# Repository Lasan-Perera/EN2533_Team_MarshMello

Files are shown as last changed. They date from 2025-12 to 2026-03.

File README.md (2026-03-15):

# Team MarshMello 
## Module: EN2533 Robot Design and Competition

## 📖 Project Overview
Our robot was developed to complete multiple challenges announced two months before the competition. These challenges included line following, maze solving, box handling, ramp climbing, dashed-line navigation, barcode detection, ball pickup, wall following, arrow-based navigation, and ball shooting. The project required significant hardware and software development, and the final robot was able to autonomously navigate the arena and successfully complete the assigned tasks.

## 🤖 Robot
file_00000000e0a47206bf88b3c999087ba9



## 🎥 Robot Task Demonstration
Robot Tasks Video (https://youtu.be/oBLyfxPuTzA)

## 🔧 Robot Hardware Specifications
- **Max Dimensions**: 200mm × 190mm  
- **Power Supply**: 4 18650 Li-ion Battries
- **Components**:
  - Arduino Mega mini Development board x1
  - Raykha S8 – TCRT5000 based 8-channel reflective sensor array x1
  - Nema 17 Stepper Motors x2
  - DRV8825 Stepper Driver x2
  - LM2596 DC-DC Buck Converter x2
  - XL4015 DC-DC Buck Converter x1
  - MG90 metal gear servo motors x3
  - MG995 Tower Pro servo motor x1
  - SHARP GP2Y0A51SK0F Infrared IR Sensor x5
  - TCS34725 RGB Colour Recognition Sensor x1
  - Obstacle Avoidance Sensor IR Infrared Module x3
  - DC Motor 380 Motor x2
  - Rotary Encoder Module with Push Button
  - 0.96″ OLED display

## 💻 Robot Software Specifications
- **Programming Language**: C++
- **IDE**: Arduino IDE
- **Libraries**:
  - Arduino.h
  - Servo.h
  - Adafruit_TCS34725.h
  - MultiStepper.h
  - AccelStepper.h
  - Wire.h
  - Adafruit_GFX
  - Adafruit_SSD1306
- **3D Modelling**: AutoDesk Fusion
- **Schemetic Design**: Altium Designer



  




## ⚙️ Mechanisms and Algorithms
### <u>Custom Motor Brackets, Wheel Rims, SHARP IR Brackets</u>



---

### <u>Balls and Box Pickup Mechanism</u>

From the beginning, we decided to use an arm mechanism to pick up balls and boxes from the side. This required precise control of the robot. We planned to store the collected balls in a container located at the top of the robot. The container had to be positioned at an appropriate height so gravity could be used to feed the balls into the ball-sending mechanism, which was a major design challenge.

To address this, we used an L-shaped arm. A high-torque servo was used for the main arm movement, while a smaller servo controlled the gripper. This combination significantly simplified the mechanism.

The gripper had to handle both balls (4 cm diameter) and boxes (5 cm wide). To achieve this, I designed a special gripper with an internal cutout. When gripping a ball, the arms move closer than usual, allowing the ball to travel upward through the rail-like cut. Since the color sensor was placed at the top, this design allowed us to take color readings effectively.

However, the initial grip was not strong enough to hold boxes securely. To improve grip, we added hot glue inside the gripper and covered it with a rubber balloon. While this solved the box-gripping issue, it prevented the ball from moving upward.

To overcome this, we implemented a control solution: after gripping the ball and raising the arm, the gripper briefly opens and closes again. This allows the ball to move closer to the color sensor. This approach worked successfully.



---

### <u>Balls Storing Mechanism</u>

The container had to be positioned at a suitable height so gravity could feed the balls into the ball-sending mechanism. The main challenge was designing a container within limited space that could store four balls while ensuring they would not block each other during release.

Later, I discovered that the original container design was approximately 5 mm lower than the required height. To fix this, I added a 5 mm thick 3D-printed spacer block in the middle of the structure.



---

### <u>Balls Shooting Mechanism</u>

The ball sender needed to launch the balls through a given hoop. We used DC motors rotating at high speed, with the ball placed between them. To achieve sufficient grip, we used two toy truck wheels attached to the motors.

Finding the correct distance between the motors required several design iterations. Another major issue was ensuring that balls were sent one at a time. If two balls entered the mechanism simultaneously, the second ball would not travel the required distance.

To solve this, I designed a blocking mechanism that prevents the next ball from entering while one ball is being launched.

Initially, we attempted to control the motors using relays, but this failed due to the high startup current. When the motors started, the relay would switch off, causing an endless on-off loop without proper motor operation. To resolve this issue, we replaced the relays with a motor driver, which worked reliably.



---

### <u>Grid Solving Algorithm</u>

The robot operates on a **Grid Navigation System** driven by a finite state machine.

- **Mapping**: Maintains an internal 8×8 coordinate grid updated in real time using wall and object detection.
- **Pathfinding**: Uses **Breadth-First Search (BFS)** to compute the shortest path to any target cell. The path is recalculated after each movement to adapt to new obstacles.
- **Mission Logic**: Controlled by a high-level **State Machine**:
  - **Search**: Snake-pattern sweep of the grid to locate boxes
  - **Pickup**: Multi-angle selector enforcing strict X-axis approach based on arm geometry
  - **Transport**: BFS-based navigation back to the sanctuary zone
  - **Avoidance**: Marks inaccessible paths and targets to prevent deadlocks

## 🚩 Competition Tasks
- **Task 1**: The Labyrinth of Shadows (Grid Solving) 
- **Task 2**: The Ramp of Trials (Creation, Ascending, and Descending Ramp)
- **Task 3**: The Oracle of Runes (Barcode Reading)
- **Task 4**: The Circular Fortress (Wall Following and Ball Collection)
- **Task 5**: The Wall of Whispers & Pendulum of Doom 
- **Task 6**: The Line of Destiny & The Ring of Triumph (Shooting Task)

**Project Documentation**
[]([path/to/your-file.pdf](https://github.com/user-attachments/files/24347659/Robot_Design_Task_2025_251226_191908.pdf)) 

## 🏟️ Arena


## 👥 Team Members
| Name | Index Number |
|---|---|
| Lasan Sanjula Perera | 230487D |
| Hasith Nettikumara | 230436X |
| Kavija Karunarathna | 230322U |
| Hiruna Kariyawasam | 230318M |
| Rusiru Anupama | 230536E |



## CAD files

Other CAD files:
3D_Files/Assembly.f3z

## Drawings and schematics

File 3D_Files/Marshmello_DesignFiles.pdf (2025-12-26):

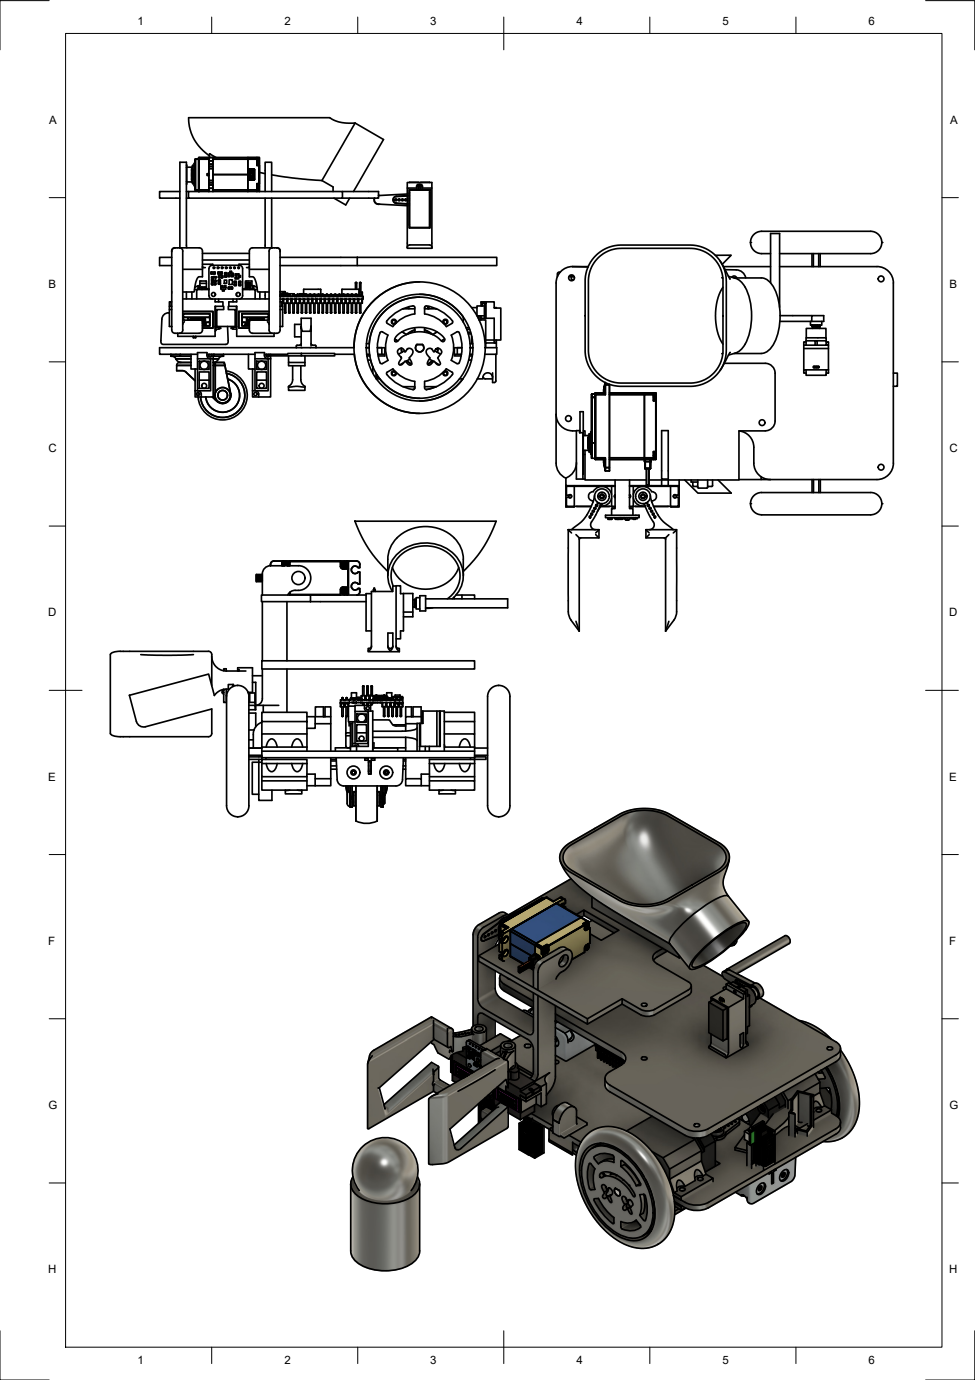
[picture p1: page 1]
6 ABCDEFGH; ABCDEFGH

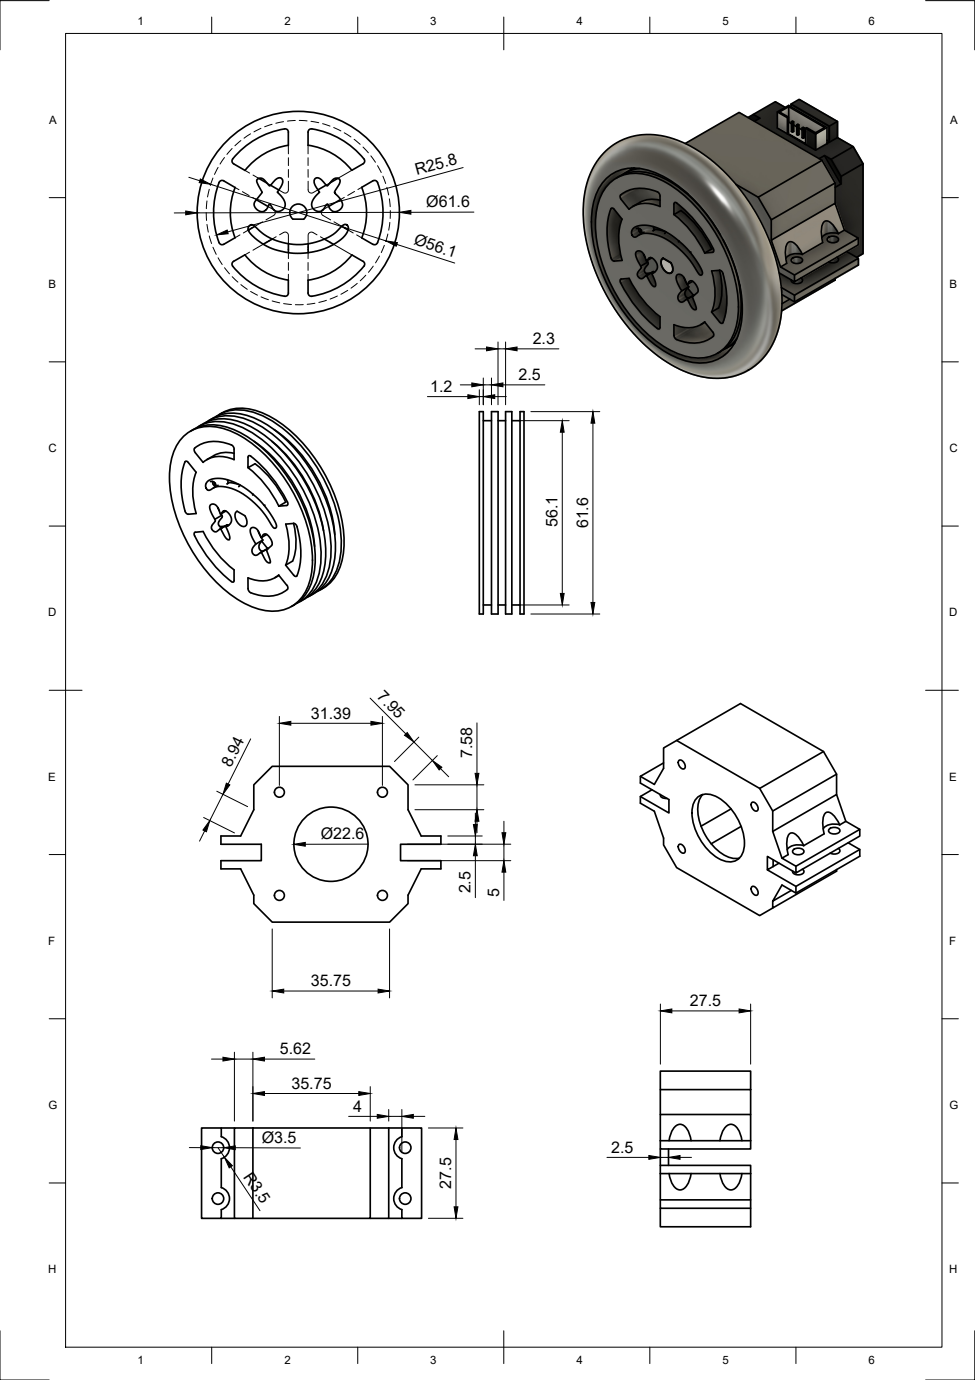
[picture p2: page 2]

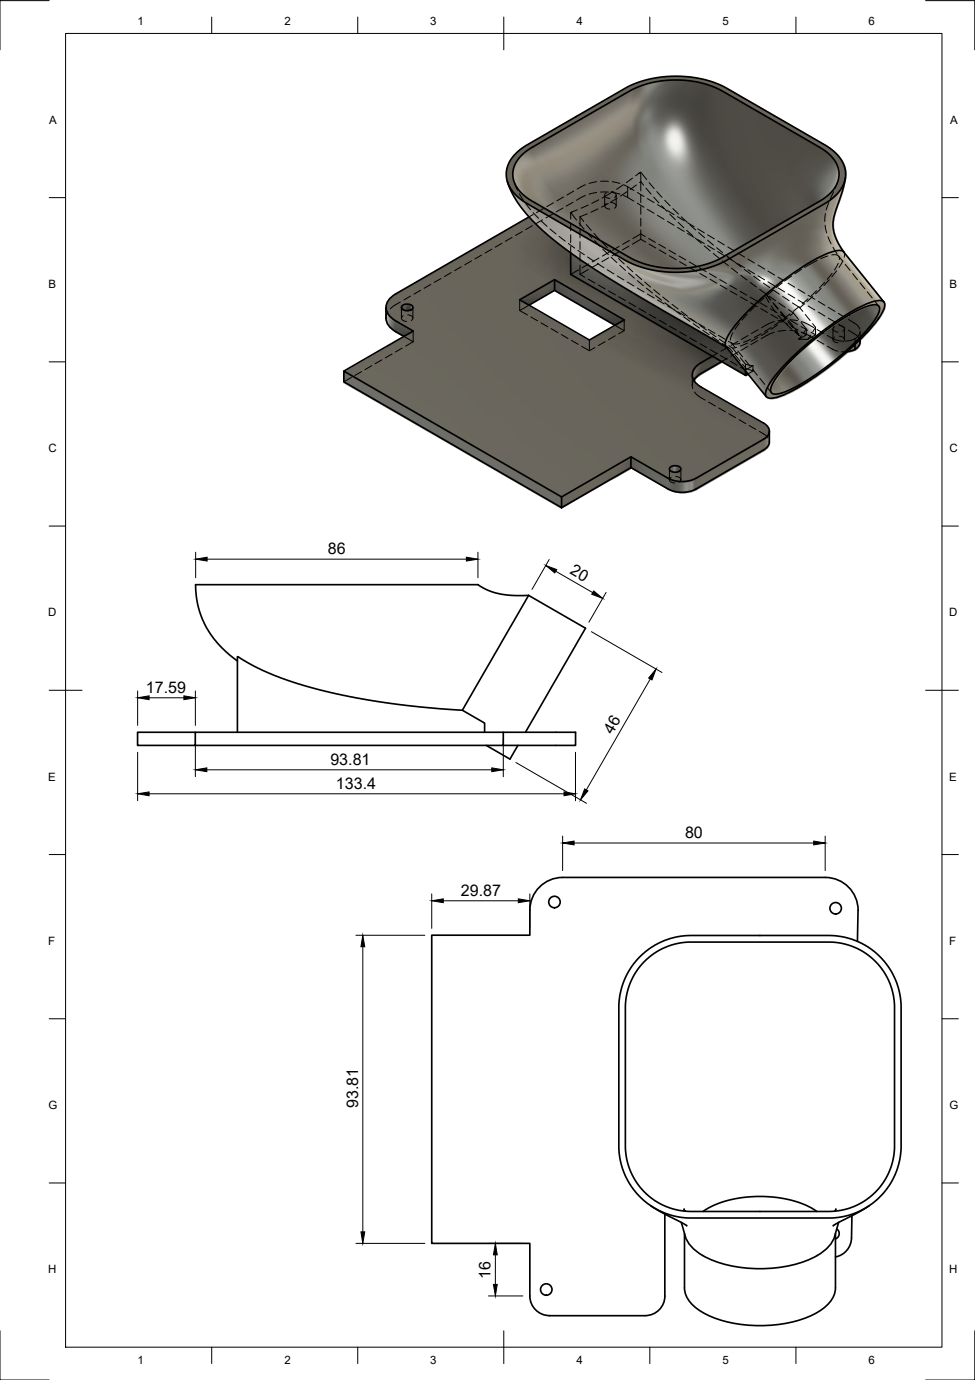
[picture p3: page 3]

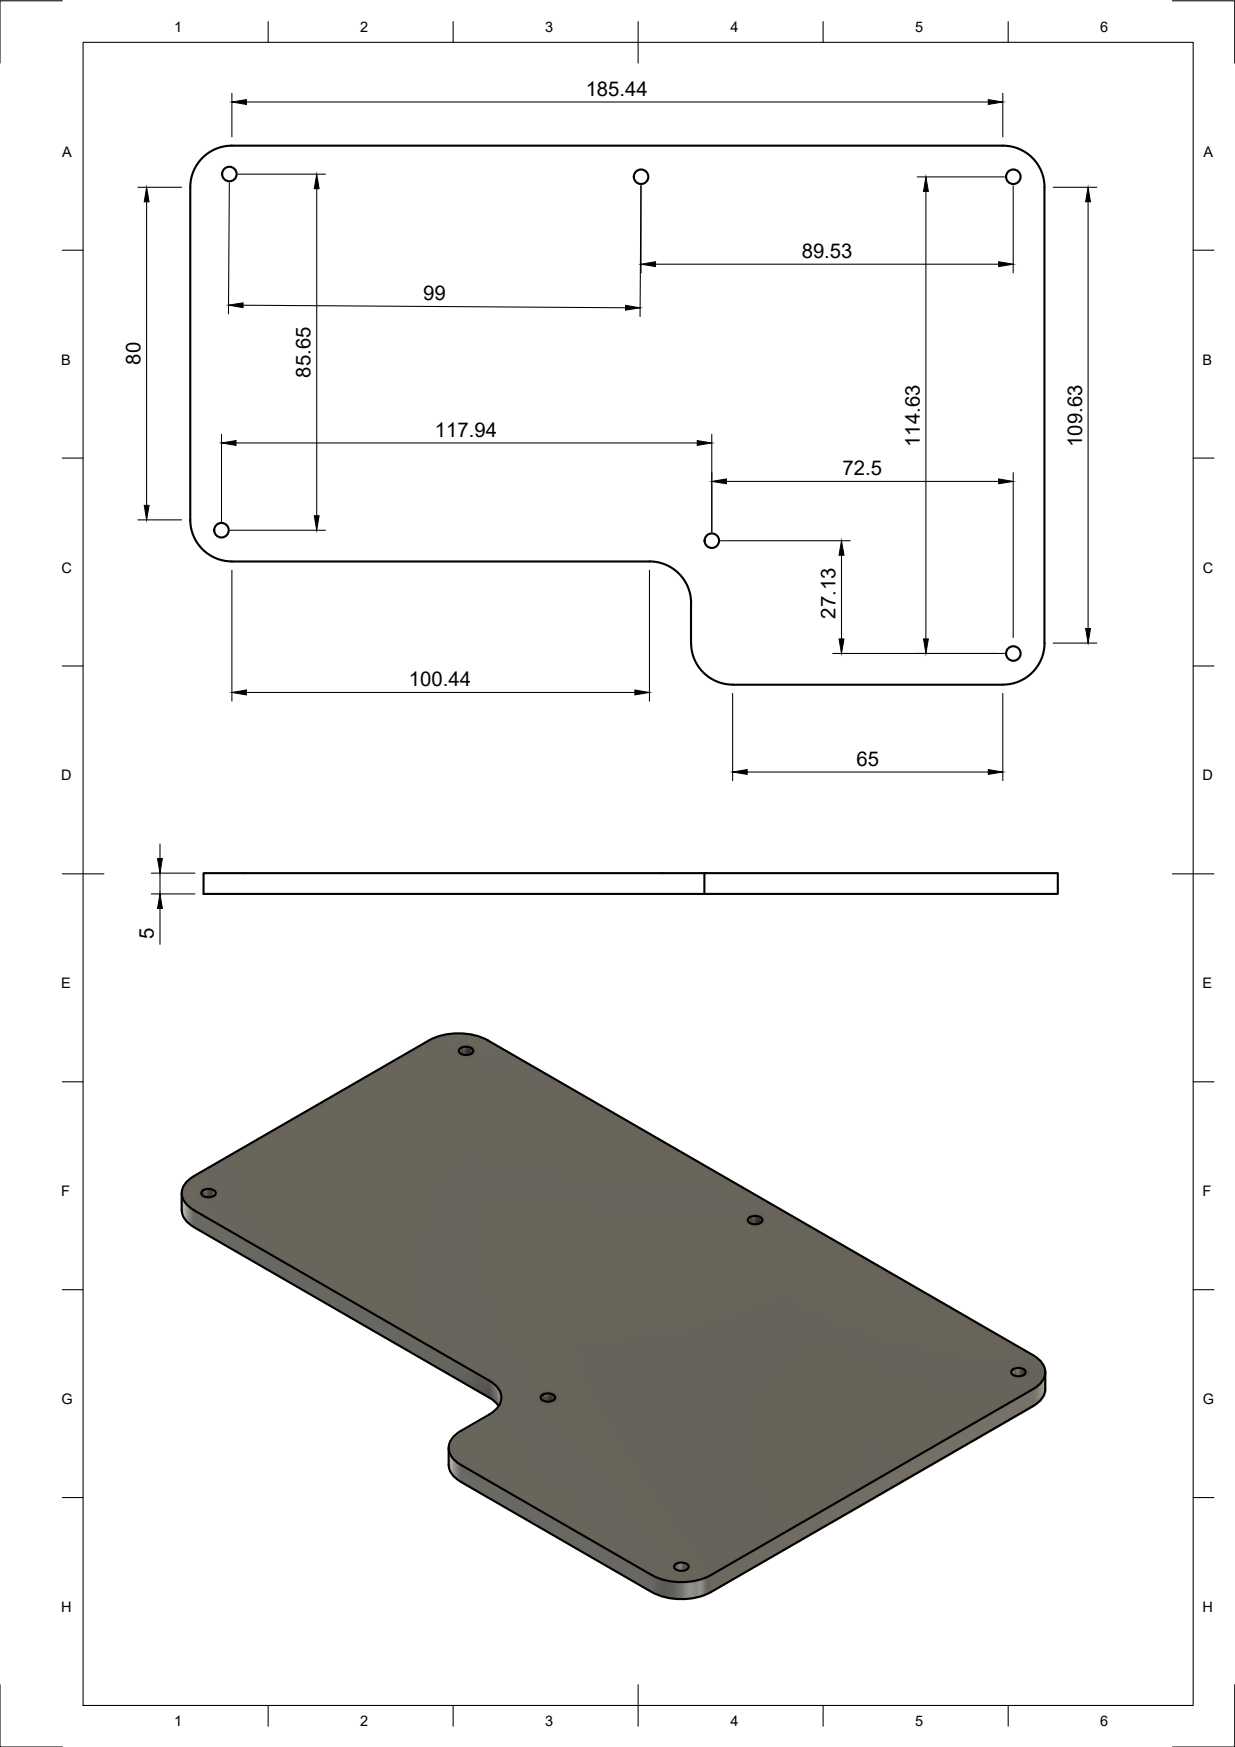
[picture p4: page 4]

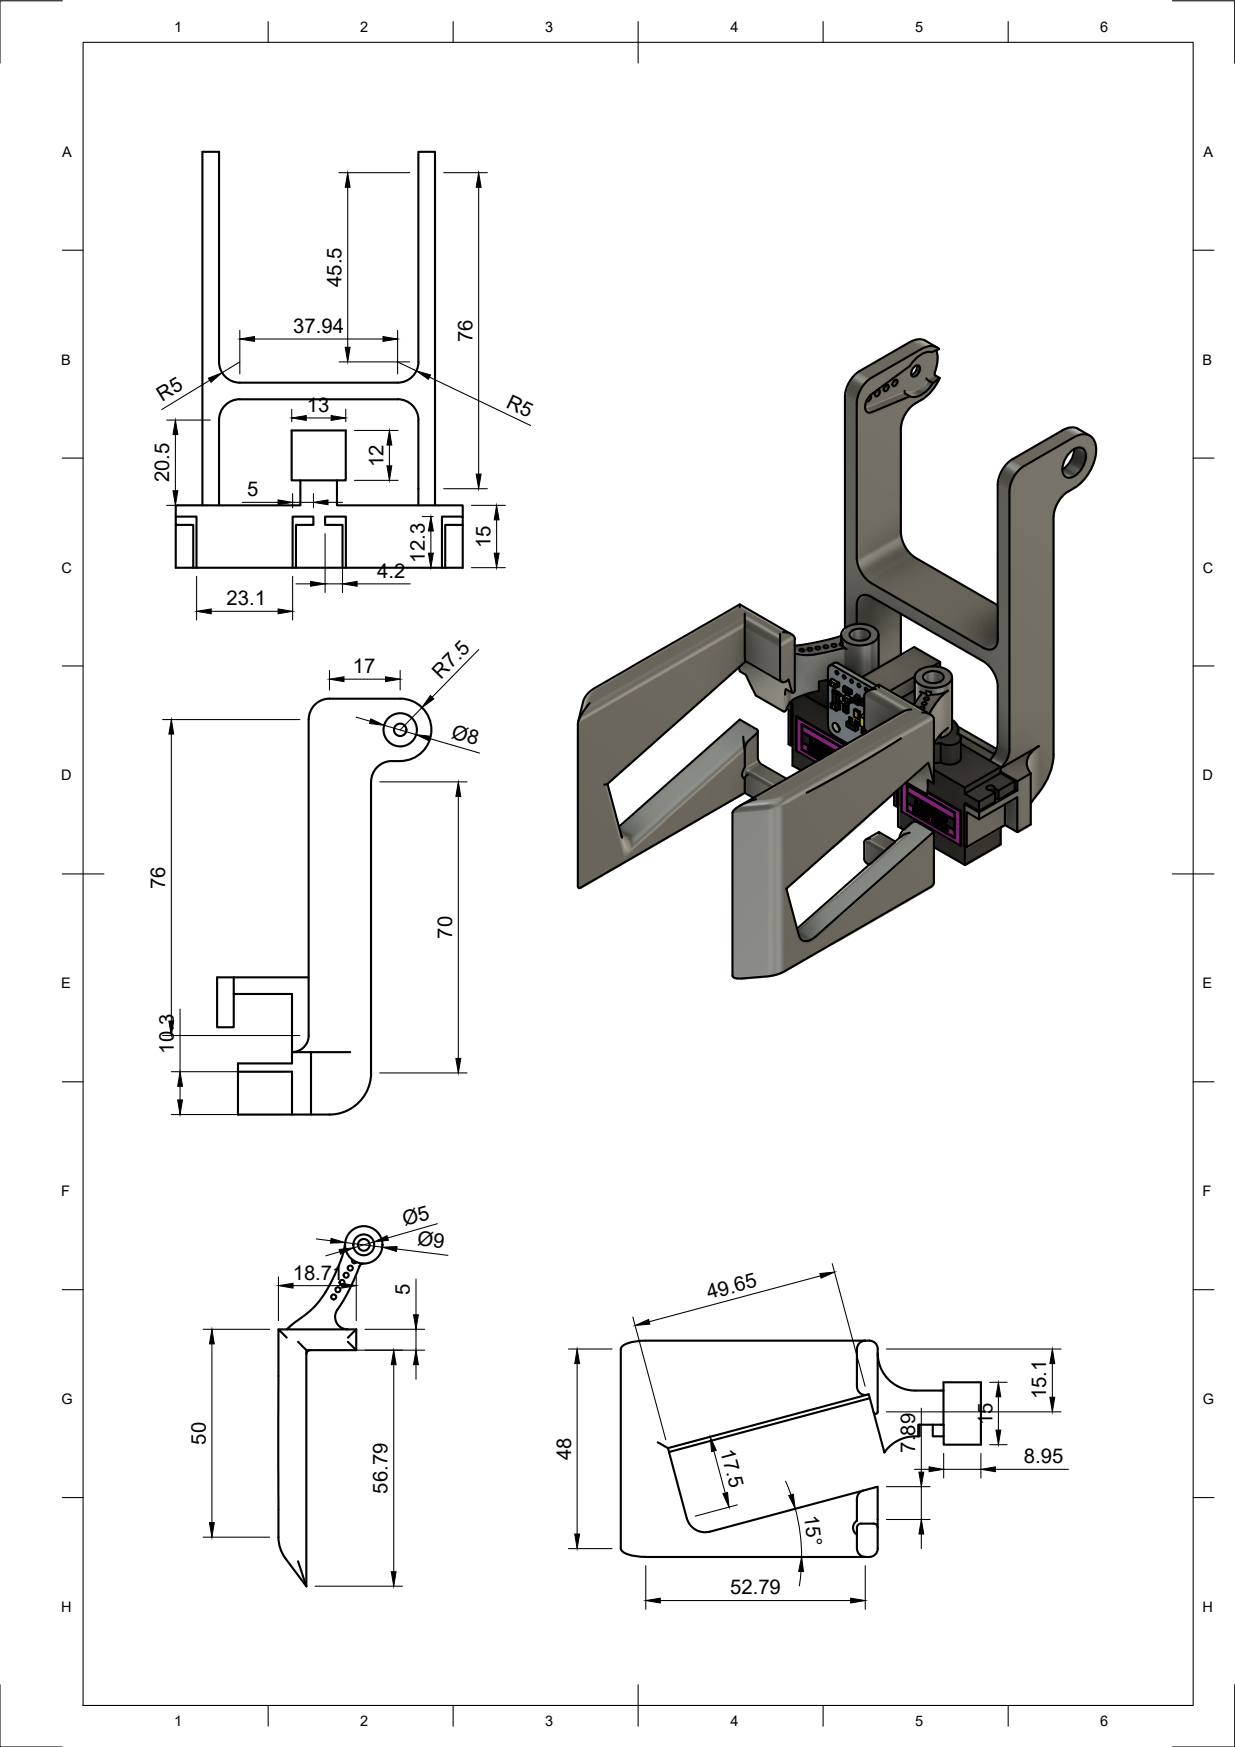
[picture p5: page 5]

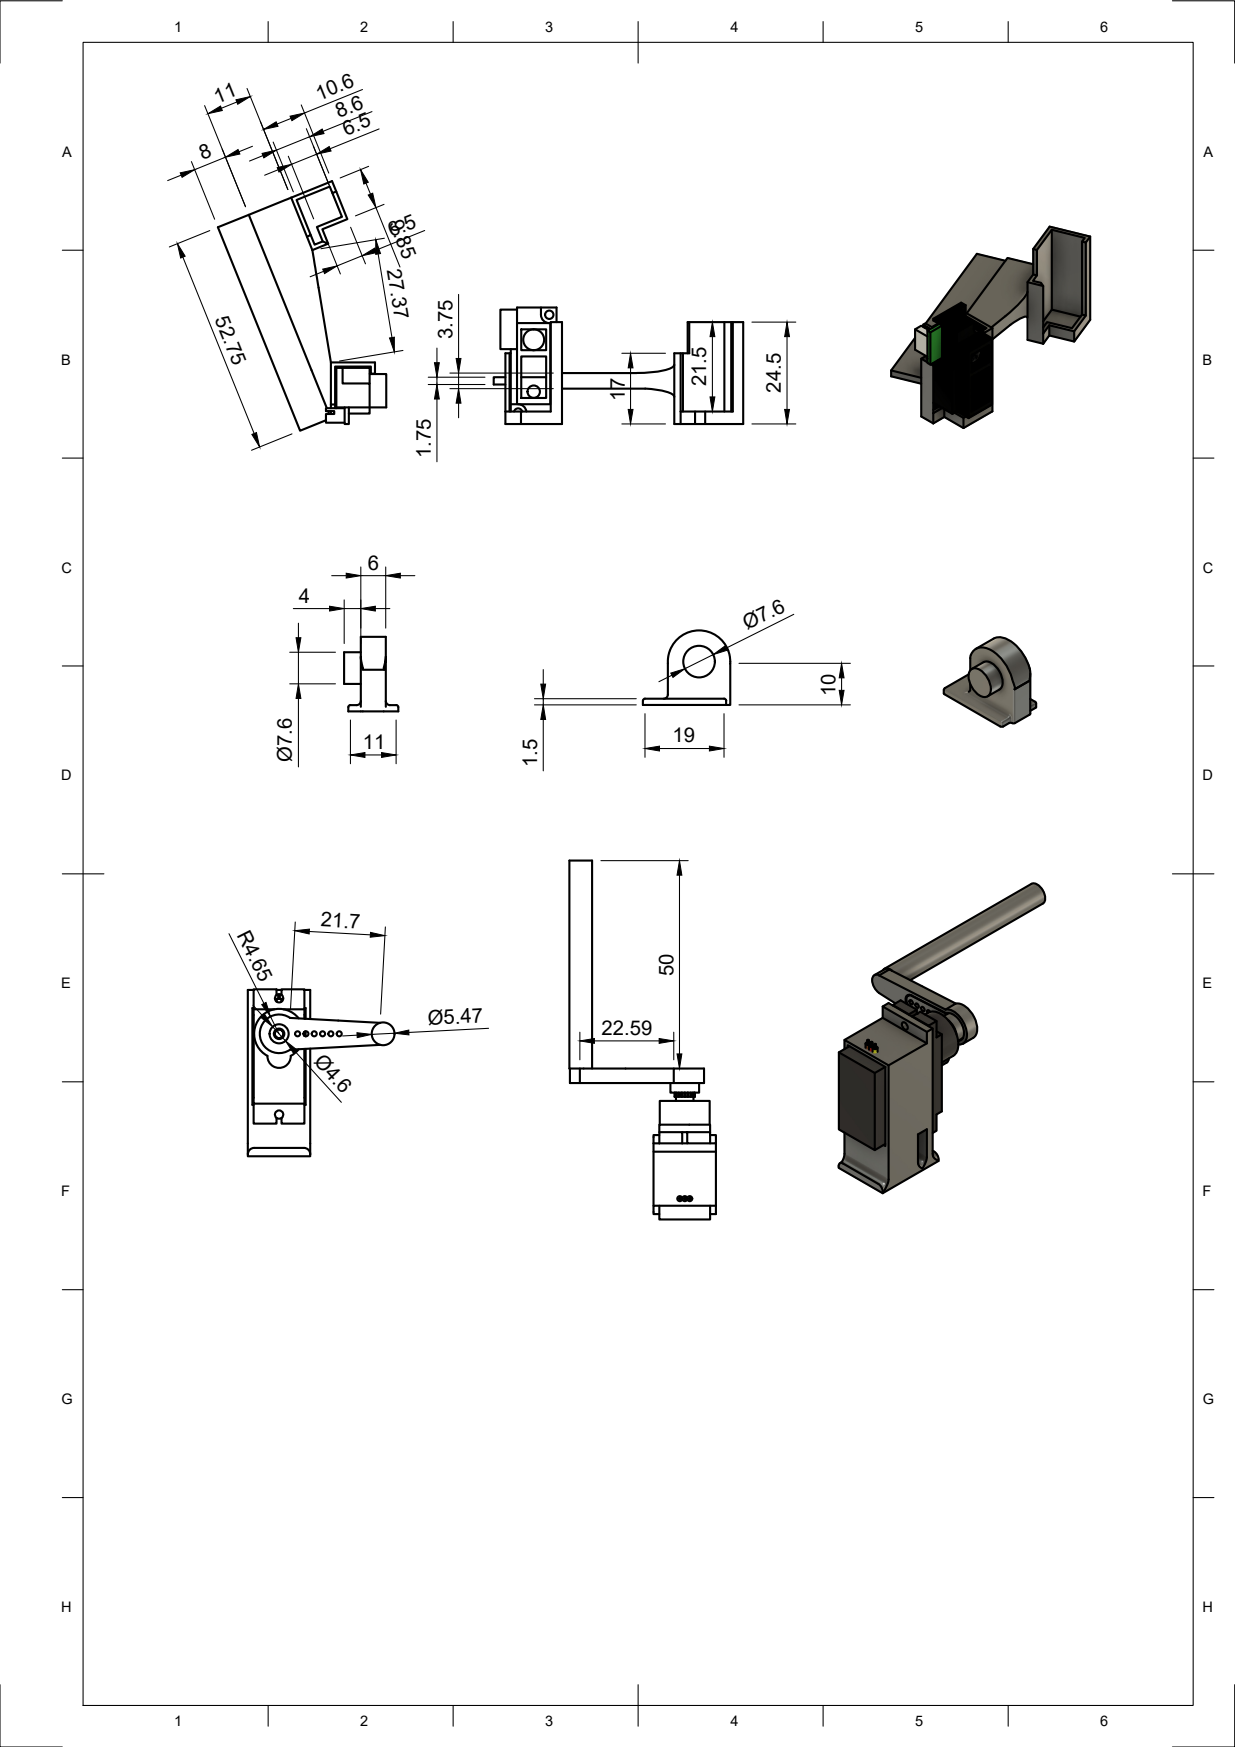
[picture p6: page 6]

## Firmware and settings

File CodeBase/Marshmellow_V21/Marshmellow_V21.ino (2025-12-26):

#include "motors.h"
#include "helperFunctions.h"
#include "sensors.h"
#include "lineFollow.h"
#include "ballCollection.h"
#include "dashLine.h"
#include "barcodeRead.h"
#include "arrowLine.h"
#include "armControl.h"
#include "ArmControlTask.h"
#include "LabyrinthTask.h"
#include "MotorControl.h"
#include "Navigation.h"
#include "RobotConfig.h"
#include "SensorsTask.h"

enum TaskMode {
  MODE_MAZE,      // normal arrow/line follow
  MODE_DASHRAMP,  // line lost, move straight until we find line again
  MODE_BARCODE,
  MODE_BALLS,
  MODE_ARROW,
  MODE_WALLS,
  MODE_SHOOT  // turning to side with more white
};

MotorControl motorControl;
SensorsTask sensors;
Navigation navigation(motorControl, sensors);
ArmControlTask armControlTask;
LabyrinthTask task(navigation, armControlTask, sensors, motorControl);
int missing;

void setup() {
  Serial.begin(115200);
  delay(500);
  
  Serial.println(">>> ROBOT INITIALIZING <<<");

  motorControl.init();
  Serial.println("HAL: Motor Control Initialized");
  motorControl.enableMotors();  // Explicit enable

  // HARDWARE TEST: Move forward 100 steps blindly to verify motors
  // Serial.println("TESTING: Move Forward 400 steps...");
  // motorControl.moveForward(400);
  // delay(1000);
  // Serial.println("TESTING: Move Backward 400 steps...");
  // motorControl.moveBackward(400);
  // delay(1000);

  sensors.init();
  Serial.println("HAL: SensorsTask Initialized");
  Serial.flush();

  armControlTask.init();
  Serial.println("HAL: Arm Control Initialized");
  armControlTask.disable();  // Detach to save power/prevent conflict

  delay(500);
  motorControl.init();
  motorControl.enableMotors();
  Serial.println("HAL: Motor Control Re-asserted");

  task.init();
  Serial.println("HAL: Task Initialized");
  Serial.flush();

  Serial.println(">>> SYSTEM READY. STARTING TASK <<<");
  setupIRSensors();
  setupDistanceSensors();
  delay(500);


  // dashLineXramp();
  // forward(300);
  // while (!isFourWay()){
  //   lineFollow90Bends(1, 0, 0);
  // }
  // resetPID();
  // forward(350);
  // right90();
  // collectBalls();
  // forward(350);
  // right90();
  // while(!isFourWay()) {
  //   arrowFollowLoop();
  // }
}


TaskMode currentMode = MODE_MAZE;
bool arrowDone = false;
bool mazeDone = false;

void loop() {
  switch (currentMode) {
    case MODE_MAZE:
      static bool calibrated = false;
      if (!calibrated) {
        task.recorrection();
        calibrated = true;
      }
      if (mazeDone) {
        missing = task.getMissingColor();
        setupMotors();
        setupIRSensors();
        // setupServos();
        setupColorSensor();
        setupDistanceSensors();
        setupArm();
        delay(1000);
        armUp();
        grabberOpen();
        forward(-800);
        gofow(-1);
        forward(700);
        left90();
        forward(500);
        currentMode = MODE_DASHRAMP;
      }
      task.run();
      mazeDone = task.taskDone();

      break;

    case MODE_DASHRAMP:
      dashLineXramp();
      currentMode = MODE_BARCODE;
      break;

    case MODE_BARCODE:
      // while (!isFourWay() && barcodeFinished()) {
      //   lineFollow(3.9, 0, 1.85);
      //   readSensors();
      //   if (!barcodeFinished()) {
      //     barcodeUpdate(sensorValues, stepperR.currentPosition());
      //   } else {
      //     sphereCount = getSphereCount();
      //   }
      // }
      // while (!isFourWay()) {
      //   if(sensorValues[0] < 300 || sensorValues[1] < 300) {
      //     right90();
      //   }
      //   // dashedLineFollow(100, 100);
      //   lineFollow(3.9, 0, 1.85);
      // }
      forward(800);
      right90();
      while (!isFourWay()) {
        lineFollow(3.9, 0, 1.85);
      }
      stopRobot();
      forward(1500);
      arm.indication();
      while (!isFourWay()) {
        lineFollow(3.9, 0, 1.85);
      }
      forward(350);
      right90();
      currentMode = MODE_BALLS;
      break;

    case MODE_BALLS:
      while (getDistance(frontIR) > 6) {
        lineFollow(3.9, 0, 1.85);
      }
      turnAngle(500);
      while (getDistance(rightStraightIR) < 15) {
        wallFollow(6, 0, 1.85, 240);
        if (getDistance(rightStraightIR) > 10) {
          stepperL.setAcceleration(1000.0);
          stepperR.setAcceleration(1000.0);
          stepperL.move(850);
          stepperR.move(350);
          while (stepperL.distanceToGo() != 0 || stepperR.distanceToGo() != 0) {
            stepperL.run();
            stepperR.run();
          }
          forward(900);
          right90();
          forward(800);
          break;
        }
      }
      collectBallsHexagon(missing);
      while (!isFourWay()) {
        wallFollow(6, 0, 2.85, 240);
      }
      stopRobot();
      forward(350);
      left90();
      while (!isFourWay()) {
        lineFollow(3.9, 0, 1.85);
      }
      forward(350);
      right90();
      currentMode = MODE_ARROW;
      break;

    case MODE_ARROW:
      arrowFollowLoop();
      break;

    case MODE_WALLS:

      break;

    case MODE_SHOOT:

      break;
  }
}

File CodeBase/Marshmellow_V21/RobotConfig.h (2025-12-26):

#ifndef ROBOT_CONFIG_H
#define ROBOT_CONFIG_H

#include <Arduino.h>

// --- Stepper Motors (AccelStepper) ---
// --- Stepper Motors (AccelStepper) ---
// Left Stepper
#define L0 45
#define L1 43
#define L2 41
#define StepPinL 39
#define DirPinL 37
#define EnPinL 47

// Right Stepper
#define R0 44
#define R1 42
#define R2 40
#define StepPinR 38
#define DirPinR 36
#define EnPinR 46

#define STEPPER_MAX_SPEED 1500
#define STEPPER_ACCELERATION 1000

// --- Line Sensor Array (8 SensorsTask) ---
// Assuming analog pins for now, adjust as needed
const uint8_t LINE_SENSOR_PINS[] = { A0, A2, A4, A6, A8, A10, A12, A14 };
#define LINE_THRESHOLD 350

// --- Sharp IR SensorsTask (Obstacle Detection) ---
#define IR_FRONT_PIN A1
#define IR_LEFT_FRONT_PIN A11
#define IR_LEFT_BACK_PIN A3
#define IR_RIGHT_FRONT_PIN A5
#define IR_RIGHT_BACK_PIN A9

// --- Height Sensor (Obstacle vs Object) ---
#define HEIGHT_SENSOR_PIN 26  // Digital pin for 14cm height sensor

// --- Servos ---
// --- Servos ---
#define SERVO_ARM_PIN 7
#define SERVO_GRIPPER_1_PIN 8
#define SERVO_GRIPPER_2_PIN 5

// --- Color Sensor (TCS34725) ---
// I2C pins (SDA, SCL) are standard on Arduino Mega (20, 21)

// --- Robot Physical Constants ---
#define WHEEL_DIAMETER_CM 8.5
#define WHEEL_BASE_CM 17
#define STEPS_PER_REV 800

// --- Grid Constants ---
#define CELL_SIZE_CM 25.0
#define LINE_WIDTH_CM 3.0

// --- Drop Locations (X, Y) ---
// Note: Use initializer list format for Point struct assignment
#define DROP_LOCATION_BLUE \
  { 2, 8 }
#define DROP_LOCATION_GREEN \
  { 4, 8 }
#define DROP_LOCATION_RED \
  { 6, 8 }

// --- Predefined Obstacles ---
struct ObstacleCoord {
  int x;
  int y;
};

// Add your static obstacles here
const ObstacleCoord PREDEFINED_OBSTACLES[] = {
  { 3, 8 }, { 5, 8 }
  // {1, 5}, // Example: Pillar at (1,5)
};

const int PREDEFINED_OBSTACLES_COUNT =
  sizeof(PREDEFINED_OBSTACLES) / sizeof(ObstacleCoord);

#endif  // ROBOT_CONFIG_H

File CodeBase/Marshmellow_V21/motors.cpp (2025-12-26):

#include "motors.h"

AccelStepper stepperL(AccelStepper::DRIVER, StepPinL, DirPinL); // Defaults to AccelStepper::FULL4WIRE (4 pins) on 2, 3, 4, 5
AccelStepper stepperR(AccelStepper::DRIVER, StepPinR, DirPinR); // Defaults to AccelStepper::FULL4WIRE (4 pins) on 2, 3, 4, 54
MultiStepper steppers;


Servo servoBig;      
Servo servoSmall1;  
Servo servoSmall2;

int baseSpeed = 1000;
int maxSpeed  = 1500;

void setupMotors() {
  pinMode(L0, OUTPUT);
  pinMode(L1, OUTPUT);
  pinMode(L2, OUTPUT);
  pinMode(DirPinL, OUTPUT);
  pinMode(EnPinL, OUTPUT);
  digitalWrite(EnPinL, 1);  //disable
  digitalWrite(L0, 0);//  1/4 
  digitalWrite(L1, 1);
  digitalWrite(L2, 0);

  pinMode(R0, OUTPUT);
  pinMode(R1, OUTPUT);
  pinMode(R2, OUTPUT);
  pinMode(DirPinR, OUTPUT);
  pinMode(EnPinR, OUTPUT);
  digitalWrite(EnPinR, 1);  //disable
  digitalWrite(R0, 0);//  1/4 
  digitalWrite(R1, 1);
  digitalWrite(R2, 0);
  stepperL.setPinsInverted(true);

  stepperL.setMaxSpeed(maxSpeed);
  stepperR.setMaxSpeed(maxSpeed);

  steppers.addStepper(stepperL);
  steppers.addStepper(stepperR);  

  digitalWrite(EnPinL, 0);
  digitalWrite(EnPinR, 0);
}

void setupServos() {
  servoBig.attach(7);
  servoSmall1.attach(8);
  servoSmall2.attach(5);

  servoBig.write(60);
  servoSmall1.write(80);
  servoSmall2.write(110);
}

void right90() {
  stepperL.setAcceleration(1000.0);  
  stepperR.setAcceleration(1000.0);
  stepperL.move(400);
  stepperR.move(-400);
  while(stepperL.distanceToGo() != 0 || stepperR.distanceToGo() != 0) {
    stepperL.run();
    stepperR.run();
  }
}

void left90() {
  stepperL.setAcceleration(1000.0);  
  stepperR.setAcceleration(1000.0);
  stepperL.move(-400);
  stepperR.move(+400);
  while(stepperL.distanceToGo() != 0 || stepperR.distanceToGo() != 0) {
    stepperL.run();
    stepperR.run();
  }
}

void turnAngle(int steps, int dir = 1) {
  stepperL.setAcceleration(1000.0);  
  stepperR.setAcceleration(1000.0);

  if (dir == 1){
    stepperL.move(0);
    stepperR.move(steps);
  } else {
    stepperL.move(steps);
    stepperR.move(0);
  }

  while(stepperL.distanceToGo() != 0 || stepperR.distanceToGo() != 0) {
    stepperL.run();
    stepperR.run();
  }
}

void forward(int steps) {
  stepperL.setAcceleration(1000.0);  
  stepperR.setAcceleration(1000.0);
  digitalWrite(DirPinL, HIGH);
  digitalWrite(DirPinR, HIGH);    
  stepperL.moveTo(stepperL.currentPosition ()+steps);
  stepperR.moveTo(stepperR.currentPosition ()+steps);
  // stepperL.move(steps);
  // stepperR.move(steps);
  while(stepperL.isRunning() ==  true || stepperR.isRunning() ==  true) {
    stepperL.run();
    stepperR.run();
  }
}

void applyMotorSpeed(float correction) {
  int leftSpeed  = baseSpeed - correction;
  int rightSpeed = baseSpeed + correction;

  leftSpeed  = constrain(leftSpeed,  -maxSpeed, maxSpeed);
  rightSpeed = constrain(rightSpeed, -maxSpeed, maxSpeed);

  stepperL.setSpeed(leftSpeed);
  stepperR.setSpeed(rightSpeed);

  stepperL.runSpeed();
  stepperR.runSpeed();
}

void applyMotorSpeed_slow(float correction) {
  int leftSpeed  = baseSpeed/2 - correction;
  int rightSpeed = baseSpeed/2 + correction;

  leftSpeed  = constrain(leftSpeed,  -maxSpeed, maxSpeed);
  rightSpeed = constrain(rightSpeed, -maxSpeed, maxSpeed);

  stepperL.setSpeed(leftSpeed);
  stepperR.setSpeed(rightSpeed);

  stepperL.runSpeed();
  stepperR.runSpeed();
}


void stopRobot() {
  stepperL.stop();
  stepperR.stop();
  stepperL.runToPosition(); 
  stepperR.runToPosition();
}


void sweepServo(Servo &s, int startAngle, int endAngle, int speed = 10) {
  if (startAngle < endAngle) {
    for (int pos = startAngle; pos <= endAngle; pos++) {
      s.write(pos);
      delay(speed);
    }
  } else {
    for (int pos = startAngle; pos >= endAngle; pos--) {
      s.write(pos);
      delay(speed);
    }
  }
}

void sweepGrabber(int start1, int end1, int start2, int end2, int steps = 1, int speed = 10) {
  int pos1 = start1;
  int pos2 = start2;

  int dir1 = (end1 > start1) ? 1 : -1;
  int dir2 = (end2 > start2) ? 1 : -1;

  while (pos1 != end1 || pos2 != end2) {
    if (pos1 != end1) pos1 += dir1;
    if (pos2 != end2) pos2 += dir2;

    servoSmall1.write(pos1);
    servoSmall2.write(pos2);
    delay(speed);
  }
}

void armDown() {
  sweepServo(servoBig, servoBig.read(), 5);
}

void armUp() {
  sweepServo(servoBig, servoBig.read(), 180);
}

void grabberOpen() {
  sweepGrabber(servoSmall1.read(), 20, servoSmall2.read(), 155, 1, 10);
}

void grabberClose() {
  sweepGrabber(servoSmall1.read(), 130, servoSmall2.read(), 45, 1, 10);
}

void leftTurn(int turnSteps = 267) {
  stepperL.setAcceleration(1000.0);
  stepperR.setAcceleration(1000.0);

  stepperL.move(-turnSteps);
  stepperR.move(+turnSteps);

  while (stepperL.distanceToGo() != 0 || stepperR.distanceToGo() != 0) {
    stepperL.run();
    stepperR.run();
  }
}

void right60() {
  stepperL.setAcceleration(1000.0);
  stepperR.setAcceleration(1000.0);

  int turnSteps = 220;  // approx 60 degrees based on 400 = 90°

  stepperL.move(+turnSteps);
  stepperR.move(-turnSteps);

  while (stepperL.distanceToGo() != 0 || stepperR.distanceToGo() != 0) {
    stepperL.run();
    stepperR.run();
  }
}

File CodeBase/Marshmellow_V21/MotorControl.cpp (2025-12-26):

#include "MotorControl.h"

MotorControl::MotorControl()
    : leftStepper(AccelStepper::DRIVER, StepPinL, DirPinL),
      rightStepper(AccelStepper::DRIVER, StepPinR, DirPinR) {}

void MotorControl::init() {
  // Initialize Control Pins
  pinMode(L0, OUTPUT);
  pinMode(L1, OUTPUT);
  pinMode(L2, OUTPUT);
  pinMode(DirPinL, OUTPUT);
  pinMode(EnPinL, OUTPUT);
  digitalWrite(EnPinL, 0); // Enable (Active LOW)
  digitalWrite(L0, 0);     // 1/4
  digitalWrite(L1, 1);
  digitalWrite(L2, 0);

  pinMode(R0, OUTPUT);
  pinMode(R1, OUTPUT);
  pinMode(R2, OUTPUT);
  pinMode(DirPinR, OUTPUT);
  pinMode(EnPinR, OUTPUT);
  digitalWrite(EnPinR, 0); // Enable (Active LOW)
  digitalWrite(R0, 0);     // 1/4
  digitalWrite(R1, 1);
  digitalWrite(R2, 0);

  Serial.println("MotorControl Initialized. Motors Enabled.");
  leftStepper.setPinsInverted(true);

  leftStepper.setMaxSpeed(STEPPER_MAX_SPEED);
  leftStepper.setAcceleration(STEPPER_ACCELERATION);
  rightStepper.setMaxSpeed(STEPPER_MAX_SPEED);
  rightStepper.setAcceleration(STEPPER_ACCELERATION);
}

void MotorControl::moveForward(long steps) {
  leftStepper.setAcceleration(STEPPER_ACCELERATION);
  rightStepper.setAcceleration(STEPPER_ACCELERATION);
  digitalWrite(DirPinL, HIGH);
  digitalWrite(DirPinR, HIGH);
  leftStepper.moveTo(leftStepper.currentPosition() + steps);
  rightStepper.moveTo(rightStepper.currentPosition() + steps);
  // stepperL.move(steps);
  // stepperR.move(steps);
  while (leftStepper.isRunning() == true || rightStepper.isRunning() == true) {
    leftStepper.run();
    rightStepper.run();
  }
}

void MotorControl::moveBackward(long steps) {
  MotorControl::moveForward(-steps);
}

void MotorControl::turnLeft(float degrees) {
  leftStepper.setAcceleration(STEPPER_ACCELERATION);
  rightStepper.setAcceleration(STEPPER_ACCELERATION);
  leftStepper.move(-400);
  rightStepper.move(+400);
  while (leftStepper.distanceToGo() != 0 || rightStepper.distanceToGo() != 0) {
    leftStepper.run();
    rightStepper.run();
  }
}

void MotorControl::turnRight(float degrees) {
  leftStepper.setAcceleration(STEPPER_ACCELERATION);
  rightStepper.setAcceleration(STEPPER_ACCELERATION);
  leftStepper.move(400);
  rightStepper.move(-400);
  while (leftStepper.distanceToGo() != 0 || rightStepper.distanceToGo() != 0) {
    leftStepper.run();
    rightStepper.run();
  }
}

void MotorControl::stop() {
  leftStepper.stop();
  rightStepper.stop();
}

void MotorControl::run() {
  leftStepper.run();
  rightStepper.run();
}

void MotorControl::runSpeed() {
  leftStepper.runSpeed();
  rightStepper.runSpeed();
}

void MotorControl::setLeftSpeed(float speed) { leftStepper.setSpeed(speed); }

void MotorControl::setRightSpeed(float speed) { rightStepper.setSpeed(speed); }

void MotorControl::applyMotorSpeed(float correction, int speed) {
  //  int baseSpeed = 1000; // Too fast for startup?
  int baseSpeed = speed; // Default was 1000, now passed in. Check Caller.//
                         // User defined base speed
  int maxSpeed = 1400;   // Increased to 1200 (was 800) for faster response

  int leftSpeed = baseSpeed - correction;
  int rightSpeed = baseSpeed + correction;

  leftSpeed = constrain(leftSpeed, -maxSpeed, maxSpeed);
  rightSpeed = constrain(rightSpeed, -maxSpeed, maxSpeed);

  leftStepper.setSpeed(leftSpeed);
  rightStepper.setSpeed(rightSpeed);

  leftStepper.runSpeed();
  rightStepper.runSpeed();
}

bool MotorControl::isRunning() {
  return leftStepper.isRunning() || rightStepper.isRunning();
}

long MotorControl::cmToSteps(float cm) { return cm * STEPS_PER_CM; }

long MotorControl::degreesToSteps(float degrees) {
  // Arc length for one wheel to turn 'degrees'
  // Arc = (degrees/360) * (PI * WheelBase)
  float turningCircumference = WHEEL_BASE_CM * PI;
  float arcLength = (degrees / 360.0) * turningCircumference;
  return cmToSteps(arcLength);
}

long MotorControl::getCurrentPosition() {
  return leftStepper.currentPosition();
}

void MotorControl::enableMotors() {
  digitalWrite(EnPinL, LOW);
  digitalWrite(EnPinR, LOW);
}

void MotorControl::disableMotors() {
  digitalWrite(EnPinL, HIGH);
  digitalWrite(EnPinR, HIGH);
}

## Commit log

2025-12-26 Adjust image size and add spacer block details
    Updated image size in README and added spacer block information.
2025-12-26 Adjust image size in README for motor brackets
    Updated image size for the second image in the mechanisms section.
2025-12-27 Revise motor control section in README
    Updated README to include information about motor control issues and solutions.
2026-02-02 upload assembly file
    [Assembly.f3z]
